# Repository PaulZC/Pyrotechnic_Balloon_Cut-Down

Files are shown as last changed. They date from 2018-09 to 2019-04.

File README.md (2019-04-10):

# Pyrotechnic Balloon Cut-Down Device

A lightweight wireless cut-down device for use on high altitude balloons.

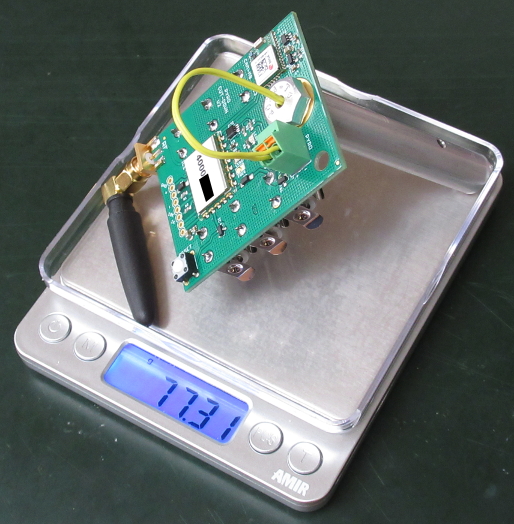
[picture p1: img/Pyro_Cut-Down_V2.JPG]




Designed to be triggered by the [Iridium Beacon Radio Board](https://github.com/PaulZC/Iridium_Beacon_Radio_Board) and equipped with an
[LPRS eRIC4 or eRIC9 integrated radio module](http://www.lprs.co.uk/products/easyradio-ism-modules/eric-soc-rf-modules.html),
the cut-down will be triggered when the eRIC receives its own (unique) serial number on the chosen channel. The number of cut-downs that could be
triggered by a single Iridium Beacon is essentially unlimited.

See [How do I configure the altitude limit](https://github.com/PaulZC/Pyrotechnic_Balloon_Cut-Down/blob/master/LEARN.md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)
for details on how to set the altitude limit using the I/O pins or via radio.

The cutter has been designed to reliably sever size 4N (2.4mm) braided nylon cord.

The cut-down device could also be used to control:
- a nichrome hot wire cord cutter
- a strobe or audible alarm
- any other device which can operate from 3.3V to 4.8V (depending on the battery voltage)

See [LEARN.md](https://github.com/PaulZC/Pyrotechnic_Balloon_Cut-Down/blob/master/LEARN.md) for further details.

See [ASSEMBLY.md](https://github.com/PaulZC/Pyrotechnic_Balloon_Cut-Down/blob/master/ASSEMBLY.md) for details on how to assemble and configure the PCB.

See [CUTTER.md](https://github.com/PaulZC/Pyrotechnic_Balloon_Cut-Down/blob/master/CUTTER.md) for details on how to assemble the mechanical parts.

See [Pyro_Cut-Down_V2.pdf](https://github.com/PaulZC/Pyrotechnic_Balloon_Cut-Down/blob/master/Pyro_Cut-Down_V2.pdf) for the schematic,
layout and Bill Of Materials.

The [Eagle](https://github.com/PaulZC/Pyrotechnic_Balloon_Cut-Down/tree/master/Eagle) directory contains the schematic and pcb design files.

The [eRIC](https://github.com/PaulZC/Pyrotechnic_Balloon_Cut-Down/tree/master/eRIC) directory contains the code for the eRIC integrated controller.

The [Drawings](https://github.com/PaulZC/Pyrotechnic_Balloon_Cut-Down/tree/master/Drawings) directory contains the drawings for the mechanical parts.

### Disclaimer

As this project involves the use of a very small quantity of smokeless gunpowder, the information contained herein should only be used by responsible adults
in full compliance with local laws and regulations regarding the purchase, transport, storage and use of smokeless powder. Follow the manufacturer's
instructions and safety information at all times. Appropriate Personal Protective Equipment must be used when handling gunpowder. Keep all parts of this
project out of the reach of children. Proceed entirely at your own risk.

The information contained herein is provided in good faith and is believed by the author to be both accurate and safe, but in no event shall the
author be liable for any injuries or damages resulting from the use of this information howsoever caused.

### Citation

If you have found this project useful and if you are able to, please cite the paper:

P. Clark et al, An open source toolkit for the tracking, termination and recovery of high altitude balloon flights and payloads, 2019 JINST 14 P04003
[DOI:10.1088/1748-0221/14/04/P04003](https://doi.org/10.1088/1748-0221/14/04/P04003)

The Accepted Manuscript is available on arXiv: http://arxiv.org/abs/1904.04321

### License

This project is distributed under a Creative Commons Attribution + Share-alike (BY-SA) licence.
Please refer to section 5 of the licence for the "Disclaimer of Warranties and Limitation of Liability".

Enjoy!

**_Paul_**

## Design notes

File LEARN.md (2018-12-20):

# Pyrotechnic Balloon Cut-Down Device

## LEARN

A lightweight wireless cut-down device for use on high altitude balloons.





Designed to be triggered by the [Iridium Beacon Radio Board](https://github.com/PaulZC/Iridium_Beacon_Radio_Board) and equipped with an
[LPRS eRIC4 or eRIC9 integrated radio module](http://www.lprs.co.uk/products/easyradio-ism-modules/eric-soc-rf-modules.html),
the cut-down will be triggered when the eRIC receives its own (unique) serial number on the chosen channel. The number of cut-downs that could be
triggered by a single Iridium Beacon is essentially unlimited.

**New for V2: the cut-down now includes a u-blox CAM-M8Q GNSS (GPS) receiver and can be configured to trigger at a pre-set altitude.**

The cutter has been designed to sever size 4N (2.4mm) braided nylon cord.

The cut-down device could also be used to control:
- a nichrome hot wire cord cutter
- a strobe or audible alarm
- any other device which can operate from 3.3V to 4.8V (depending on the battery voltage)

See [Pyro_Cut-Down_V2.pdf](https://github.com/PaulZC/Pyrotechnic_Balloon_Cut-Down/blob/master/Pyro_Cut-Down_V2.pdf) for the schematic,
layout and Bill Of Materials.

See [ASSEMBLY.md](https://github.com/PaulZC/Pyrotechnic_Balloon_Cut-Down/blob/master/ASSEMBLY.md) for details on how to assemble and configure the PCB.

The [Eagle](https://github.com/PaulZC/Pyrotechnic_Balloon_Cut-Down/tree/master/Eagle) directory contains the schematic and pcb design files.

The [eRIC](https://github.com/PaulZC/Pyrotechnic_Balloon_Cut-Down/tree/master/eRIC) directory contains the code for the eRIC integrated controller.

See [CUTTER.md](https://github.com/PaulZC/Pyrotechnic_Balloon_Cut-Down/blob/master/CUTTER.md) for details on how to assemble the mechanical parts.

The [Drawings](https://github.com/PaulZC/Pyrotechnic_Balloon_Cut-Down/tree/master/Drawings) directory contains the drawings for the mechanical parts.

### eRIC

The heart of the Cut-Down Device is the eRIC4 or eRIC9 [easyRadio Integrated Controller](http://www.lprs.co.uk/products/easyradio-ism-modules/eric-soc-rf-modules.html).

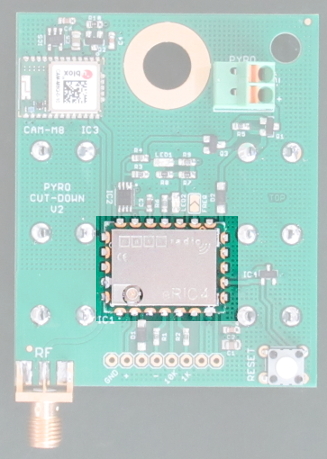
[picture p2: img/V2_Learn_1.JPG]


Either an eRIC4 or an eRIC9 can be installed. The eRIC4 operates at 402-470 MHz for Europe, APAC and China. The eRIC9 operates at 804-940 MHz for Europe,
North & South America, India and China. Solder the _FREQ_ split pad to select the eRIC9 915 MHz band.

Each eRIC has a unique serial number. The custom code running on the eRIC will trigger the cut-down when it receives a data packet containing that serial number.

The cut-down _PYRO_ output will be enabled when the eRIC receives:
- Its serial number
- Or its serial number followed by a "1"

Or, when it reaches the pre-configured altitude limit.

The cut-down output will be disabled when the eRIC receives:
- Its serial number followed by a "0"

If the serial number of the eRIC is _12345678_, the cut-down will be triggered when the eRIC receives either:
- _12345678_

or
- _123456781_

The cut-down output will be disabled when the eRIC receives:
- _123456780_

If you are using the [Iridium Beacon](https://github.com/PaulZC/Iridium_9603_Beacon) and the
[Iridium Beacon Radio Board](https://github.com/PaulZC/Iridium_Beacon_Radio_Board) to control the cut-down, you will need to send the commands:
- _[RADIO=12345678]_ or _[RADIO=123456781]_ to trigger the cut-down
- _[RADIO=123456780]_ to disable the cut-down

### u-blox CAM-M8Q

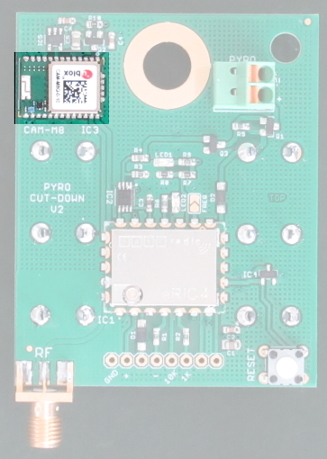
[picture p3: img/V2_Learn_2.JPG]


The cut-down is equipped with a u-blox CAM-M8Q GNSS (GPS) receiver which provides accurate altitude data.
To save power, the CAM-M8Q is configured to use only GPS satellites and ignores GLONASS, Galileo and BeiDou satellites.
Once the receiver has established a fix, the CAM-M8Q is put into low power mode to further extend the battery life.
The CAM-M8Q can be disabled by setting the altitude limit to 99km.

See [How do I configure the altitude limit](https://github.com/PaulZC/Pyrotechnic_Balloon_Cut-Down/blob/master/LEARN.md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)
below for details on how to set the altitude limit using the I/O pins or via radio.

### Pyrotechnic output

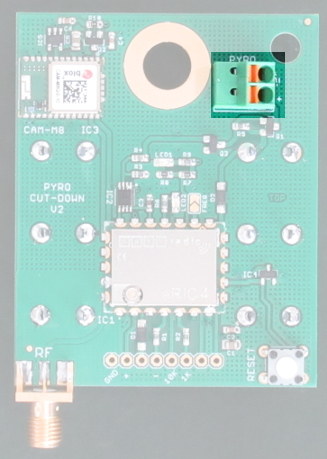
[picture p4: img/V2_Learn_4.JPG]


Q1 is a DMG3415U-7 P-Channel MOSFET which can switch currents of: 4 Amps continuous; 30 Amps pulsed. By default, the Gate of Q1 is held high by R5, which disables
the MOSFET. When the Gate of Q1 is pulled low by Q3, the full battery voltage is connected to the _PYRO+_ terminal, which triggers the electric
match within the pyrotechnic cutter.

Q3 is an NPN transistor. By default, the Base of Q3 is pulled low by R3, which disables the transistor and prevents it from pulling the Gate of Q1 low.
Q3 is enabled when the _FIRE_ signal connected to its Base goes high.

### Dual NOR gate

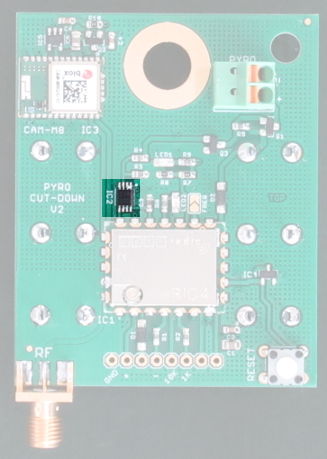
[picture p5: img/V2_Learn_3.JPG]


IC2 is a 7402 dual NOR logic gate. It prevents the _FIRE_ signal from accidentally going high, e.g. when the eRIC goes through a power-up reset. _FIRE_ can only
go high if:
- eRIC Pin17 is high (which provides power to the NOR gates)
- eRIC Pin18 is high
- eRIC Pin19 is low

The Input/Output pins on most microcontrollers go into a floating (high impedance) state during reset and can only be configured as outputs once the
embedded code starts to execute. The 7402 NOR gate ensures that _FIRE_ does not accidentally go high during that period.

### Reset supervisor

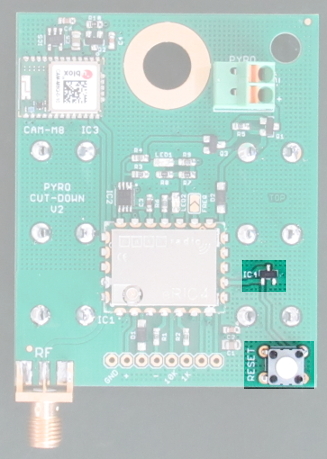
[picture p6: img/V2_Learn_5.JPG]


IC4 is an MCP111T-240 reset supervisor. It ensures that the eRIC is reset whenever the battery voltage falls below 2.4V.

Normally, the nichrome heating wire inside the electric match will go open-circuit as soon as the match is activated. If this fails to happen, Q1 will continue to
deliver current to the electric match until the batteries are exhausted. IC4 ensures that the eRIC is reset when the battery voltage starts to fall, which in turn
will disable Q1 via IC1 and Q3.

### LEDs

LED1 will illuminate when the PYRO output is active.

LED2 will flash once per second to show that the cut-down is operational. LED2 will be lit continuously when the eRIC is in bootloader mode.

### Diodes

D1 and D2 provide protection for the batteries and USB power pin from each other.

### I/O pins

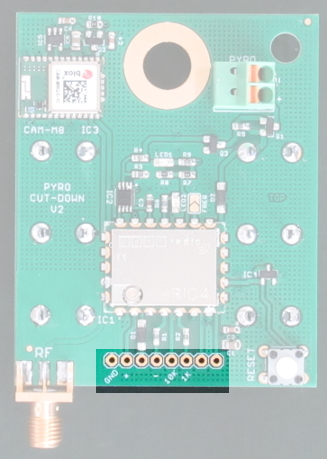
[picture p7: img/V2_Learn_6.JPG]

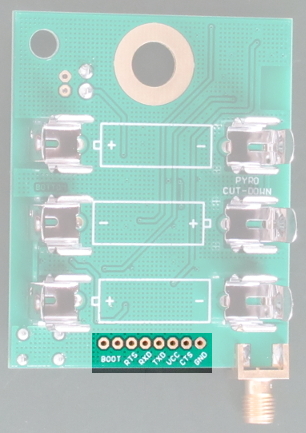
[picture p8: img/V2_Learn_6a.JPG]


The eRIC TxD, RxD, CTS and RTS pins are connected to 0.1" pads on the edge of the circuit board. The order of these pads matches the order of the pins of an FTDI
TTL-232R-3V3 USB to TTL serial cable. The eRIC can be reprogrammed via the FTDI cable.

Two extra pads are connected to the eRIC bootloader pins (Pin11 and Pin12). The eRIC will enter bootloader mode if these pads are shorted together on reset
or power-up. LED2 will be lit continuously when the eRIC is in bootloader mode.

### Antennas

Recommended antenna for the eRIC4 is:
- LPRS ANT-SR433 (Farnell part 2096221)

Recommended antenna for the eRIC9 is:
- LPRS ANT-SR900 (Farnell part 2096219)

http://www.lprs.co.uk/products/antennas-cables-connectors/stubby-antennas.html

The horizontal antenna orientation is important if the cut-down is positioned directly above the Iridium Beacon Radio Board on the balloon cord.

## How do I configure the altitude limit?

There are two methods to set the altitude limit: using the I/O pins; or via a radio message:

### Setting the Altitude Limit using the I/O pins:

The code enters Set_Altitude mode if the eRIC comes out of reset with the GND and PLUS pins connected together:
- Use a jumper wire to connect the GND and PLUS pins together;
- then press and release the RESET switch;
- then remove the jumper wire.
- The device will then enter Set_Altitude mode.



LED2 will flash three times to show that the digit three is selected.

Connect one end of the jumper wire to GND. Connect the other end to:
- MINUS to decrement the digit by one.
- PLUS to increment the digit by one.
- the 10K pin to store the digit as the altitude limit tens of kilometers.
- the 1K pin to store the digit as the altitude limit units of kilometers.

In the animation, the sequence of events is:
- The GND and PLUS pins are linked together
- The RESET switch is pressed and released
- The wire link is removed
- The cut-down is now in Set_Altitude mode
- The LED flashes three times to show the digit three
- The wire link is used to connect MINUS to GND once
- The LED flashes twice to show the digit two
- The wire link is used to connect 10K to GND once
- Two is stored in the altitude limit tens of kilometers and the LED gives a long flash
- The wire link is used to connect MINUS to GND once
- The LED flashes once to show the digit one
- The wire link is used to connect MINUS to GND once
- The LED stops flashing to show the digit zero
- The wire link is used to connect 1K to GND once
- Zero is stored in the altitude limit units of kilometers and the LED gives a long flash
- The altitude limit is now 20km
- The RESET switch is pressed and released
- The cut-down goes into normal operation
- The LED flashes twice, followed by a long flash, to indicate the altitude limit is 20km

The eRIC will stay in Set_Altitude mode until reset. Always reset the eRIC to start normal operation.

To disable the altitude limit, set it to 99km. This causes the CAM-M8Q GNSS receiver to be switched completely off,
significantly extending the battery life.

### Setting the Altitude Limit using a Radio Message:

Each eRIC has a unique serial number. The custom code running on the eRIC will set the altitude limit when it receives a data packet containing:
the eRIC serial number; followed by a "2"; followed by two digits which represent the altitude limit is kilometres.

If the serial number of the eRIC is _12345678_, an altitude limit of 33km (33000m) will be set when the eRIC receives:
- _12345678233_

If you are using the [Iridium Beacon](https://github.com/PaulZC/Iridium_9603_Beacon) and the
[Iridium Beacon Radio Board](https://github.com/PaulZC/Iridium_Beacon_Radio_Board) to control the cut-down, you will need to set the altitude limit via a RADIO command.

If you want to set the altitude limit to 33km (33000m), send:
- _[RADIO=12345678233]_

To set the altitude limit to 1km (1000m), send:
- _[RADIO=12345678201]_

The altitude limit can be disabled by setting it to 99km. This causes the CAM-M8Q GNSS receiver to be switched completely off, significantly extending the battery life.
Send:
- _[RADIO=12345678299]_

The altitude limit can be re-enabled by setting it to anything other than 99km.

## The LED flashes when I connect the batteries or reset the eRIC. Why?

When the batteries are connected or the reset switch is pressed, the cut-down goes into normal operation. The LED flashes to indicate the altitude limit. The default is
33km so the LED will flash three times, pause, then flash three times again.

A zero is indicated by a long flash. Two flashes followed by a long flash indicates an altitude limit of 20km.
A long flash followed by one flash indicates a limit of 1km.

To test that the CAM-M8Q is operating correctly, try setting an altitude limit of 0km (indicated by two long flashes).
The PYRO output and LED1 will be enabled as soon as a GPS signal is acquired (unless you are below sea level!).

## How much does it weigh?



The total weight of the assembled cut-down is 77.3 grams. This comprises:
- Assembled cutter: 27.2g
- Energiser® Ultimate Lithium AAA batteries: 22.7g
- Assembled circuit board: 21.0g
- Antenna: 6.4g

## Which AAA batteries should I use?
Energiser® Ultimate Lithium batteries. These are rated down to -40°C but tests I've done (using dry ice) show that they continue to work much colder than that.

## How long will the batteries last?

With the CAM-M8Q disabled, the average current draw is 4.6mA at 4.5V. When powered by three Energiser® Ultimate Lithium AAA batteries, the batteries
should last approximately 10 days. This ignores the current drawn by the electric match when the cut-down is activated.

With the CAM-M8Q enabled, the battery life will be reduced to approximately 2 days.

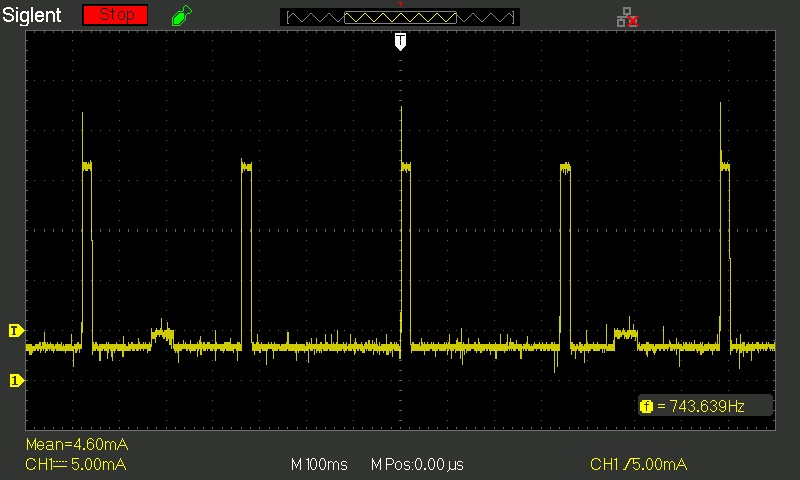
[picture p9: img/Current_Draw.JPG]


## Do I need to be careful around the battery clips?

Yes! The clips are of course conductive. If you place the circuit board battery-side down on a conductive surface **BAD THINGS WILL HAPPEN!**

## Have you tested it?

Yes. The cutter has been used successfully to sever size 4N (2.4mm) braided nylon cord with test loads of 2kg and 100g.

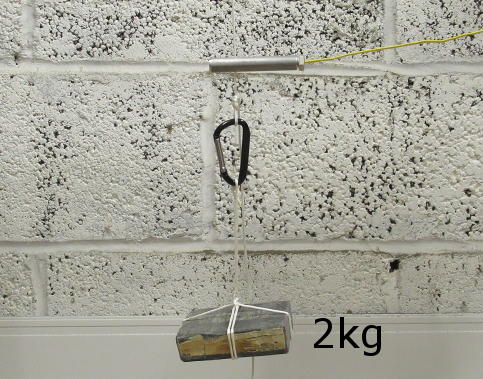
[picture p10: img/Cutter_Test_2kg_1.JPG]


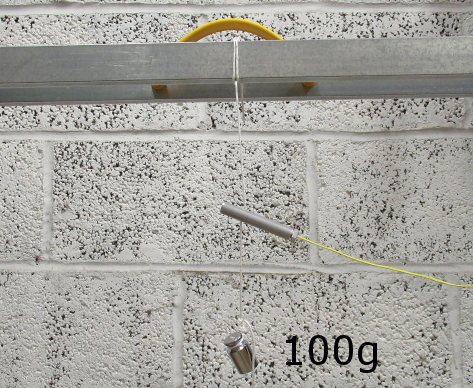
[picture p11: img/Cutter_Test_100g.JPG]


## License

This project is distributed under a Creative Commons Attribution + Share-alike (BY-SA) licence.
Please refer to section 5 of the licence for the "Disclaimer of Warranties and Limitation of Liability".

Enjoy!

**_Paul_**

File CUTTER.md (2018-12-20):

# Pyrotechnic Balloon Cut-Down Device

## Cutter Assembly

A lightweight wireless cut-down device for use on high altitude balloons.

The cutter has been designed to reliably sever size 4N (2.4mm) braided nylon cord.



### Drawings

The [Drawings](https://github.com/PaulZC/Pyrotechnic_Balloon_Cut-Down/tree/master/Drawings) directory contains the drawings for the mechanical parts plus an
assembly drawing.

### Use and Storage

Prepare the cutter as close as possible to the time of your flight, to minimise the possibility of the powder becoming damp.

If this is not possible, store the assembled cutter in a sealed box with a large sachet of fresh dessiccant.

### Prepare the Electric Match

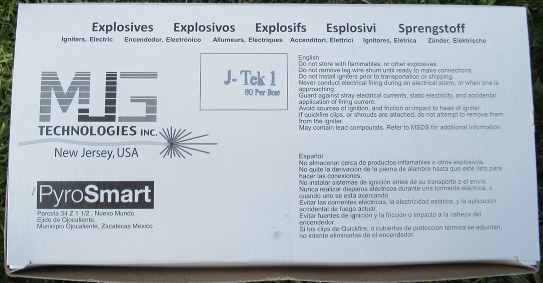
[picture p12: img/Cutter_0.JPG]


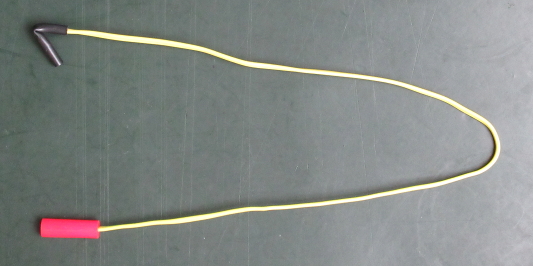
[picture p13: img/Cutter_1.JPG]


The cutter is ignited by an [MJG Technologies J-Tek1 igniter](https://electricmatch.com/pyrotechnics/see/9/5/j-tek-igniter). Made in the USA, these
are readily available from fireworks display suppliers in many countries including the UK. Technical information is available on the
[MJG Technologies website](https://electricmatch.com/upload/JTEK_TECHNICAL_INFORMATION_SHEET_SPECIFICATIONS.PDF).

The igniter contains a 1.0 ohm nichrome wire which, when heated by a current of 1 Amp or more, ignites the pyrotechnic 'match head'. The J-Tek1 can be
triggered by a single AAA alkaline battery.

Remove the black protective cover from the end of the igniter wires and ensure the bare copper wires are twised securely together. This shorts the
igniter, preventing it from being ignited accidentally by a static discharge.

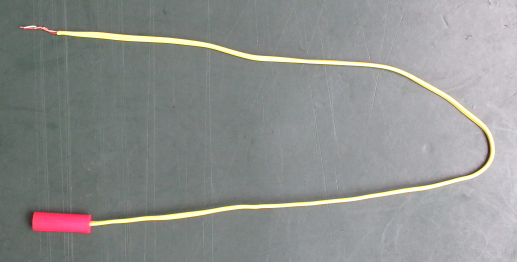
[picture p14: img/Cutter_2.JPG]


Remove the red plastic cover by pushing it off the match head and sliding it along the wire.

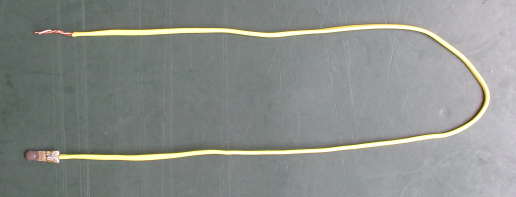
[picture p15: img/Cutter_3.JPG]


Slide a McMaster 1173N004 silicone o-ring (0.070" internal diameter) along the igniter wire until it almost touches the solder joint. This o-ring will
help prevent the gas from the powder escaping through the hex head screw.

Slide a McMaster 1173N005 silicone o-ring (0.101" ID) over the match head as shown in the assembly drawing. This o-ring will prevent the igniter from making
electrical contact with the conductive aluminium cutter body.

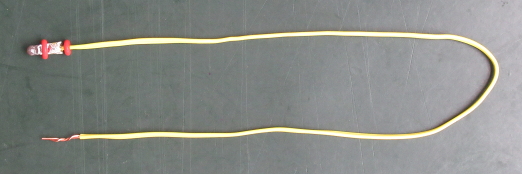
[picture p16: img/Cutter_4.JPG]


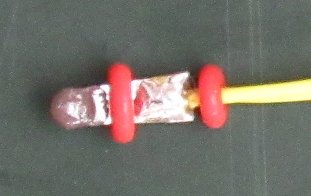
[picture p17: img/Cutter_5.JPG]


Poke the bare ends of the wires through a McMaster 93306A580 aluminium hex head screw, which has been drilled through with a 7/64" (2.8mm) drill bit. Slide the
screw along the wires until it touches the smaller o-ring.

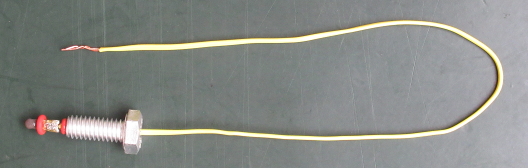
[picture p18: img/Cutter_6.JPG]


Keep the igniter wires shorted together until the cutter is complete and you are ready to connect it to the cut-down circuit board.

### Add the Smokeless Powder

Check that the inside of the cutter body is clean, dry and free from debris. Clean it with a cotton swab dipped in alcohol (rubbing alcohol or Isopropyl
Alcohol (IPA)) if required. Use a size F reamer (McMaster 89485A46) by hand to clear any stubborn deposits or burrs from the cord holes.

Insert a paper clip through the cord holes and bend it to prevent it falling out.

Slide a clean McMaster 98105A090 dowel pin into the cutter body, inserting the flatter end first. The paper clip prevents the dowel pin from sliding past the cord
holes.

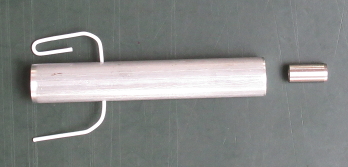
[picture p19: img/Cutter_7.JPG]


Stand the cutter body upright and using a small funnel (normally used to refill perfume bottles), pour 1.5 grains (0.10 grams) of smokeless powder into the cutter
body so it ends up on top of the dowel pin. Ensure the funnel is clean and dry before use. 0.10 grams of powder is the same amount found inside a Fiocchi 8mm NIK
starting pistol blank.

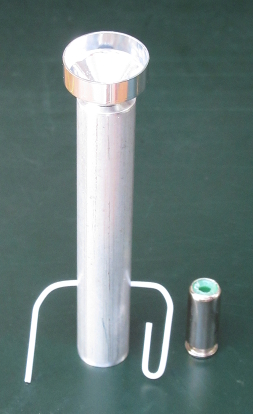
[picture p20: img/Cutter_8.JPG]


### Assemble the Cutter

Feed the igniter assembly through the cut-down circuit board and then screw it carefully into the cutter body. Orient the holes in the cutter body so they
are vertical with respect to the circuit board, then tighten the screw using a spanner. Do not overtighten the screw.

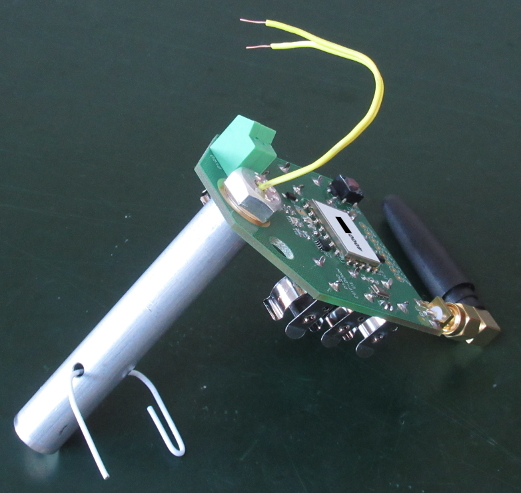
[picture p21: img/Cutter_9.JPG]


### Connect the Cutter

Cut the igniter wires short. Part the wires and remove 5mm of insulation from the end of each wire. Push the bare wire ends into the green terminal block
on the cut-down circuit board. You do not need to press the orange levers on the terminal block while you do this. The levers only need to be pressed when
releasing the wires.

Your cutter is ready for use.

You may need to melt and shape the cut end of the nylon cord so it will slide easily through the cord holes.

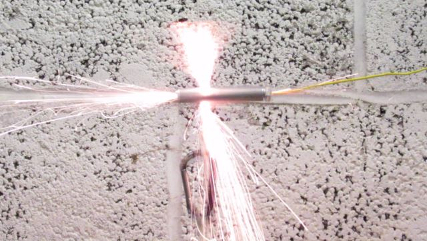
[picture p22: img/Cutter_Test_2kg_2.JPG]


### Reuse

After use, the dowel pin will end up trapped at the end of the cutter body, almost certainly jammed in place by remnants of nylon cord. You may need to drive
a parallel pin punch (McMaster 3416A24) into the hole in the end of the cutter body to release it. Take care to hold the pin punch on axis so as not to damage
the reamed bore of the cutter body.

Clean the dowel pin with cotton wool dipped in alcohol (rubbing alcohol or IPA). Clean the cutter body with a cotton swab dipped in alcohol.

Use a size F reamer (McMaster 89485A46) by hand to clear any stubborn deposits or burrs from the cord holes.

Use new o-rings each time even if they look intact.

### Disclaimer

As this project involves the use of a very small quantity of smokeless gunpowder, the information contained herein should only be used by responsible adults
in full compliance with local laws and regulations regarding the purchase, transport, storage and use of smokeless powder. Follow the manufacturer's
instructions and safety information at all times. Appropriate Personal Protective Equipment must be used when handling gunpowder. Keep all parts of this
project out of the reach of children. Proceed entirely at your own risk.

The information contained herein is provided in good faith and is believed by the author to be both accurate and safe, but in no event shall the
author be liable for any injuries or damages resulting from the use of this information howsoever caused.

### License

This project is distributed under a Creative Commons Attribution + Share-alike (BY-SA) licence.
Please refer to section 5 of the licence for the “Disclaimer of Warranties and Limitation of Liability”.

Enjoy!

**_Paul_**

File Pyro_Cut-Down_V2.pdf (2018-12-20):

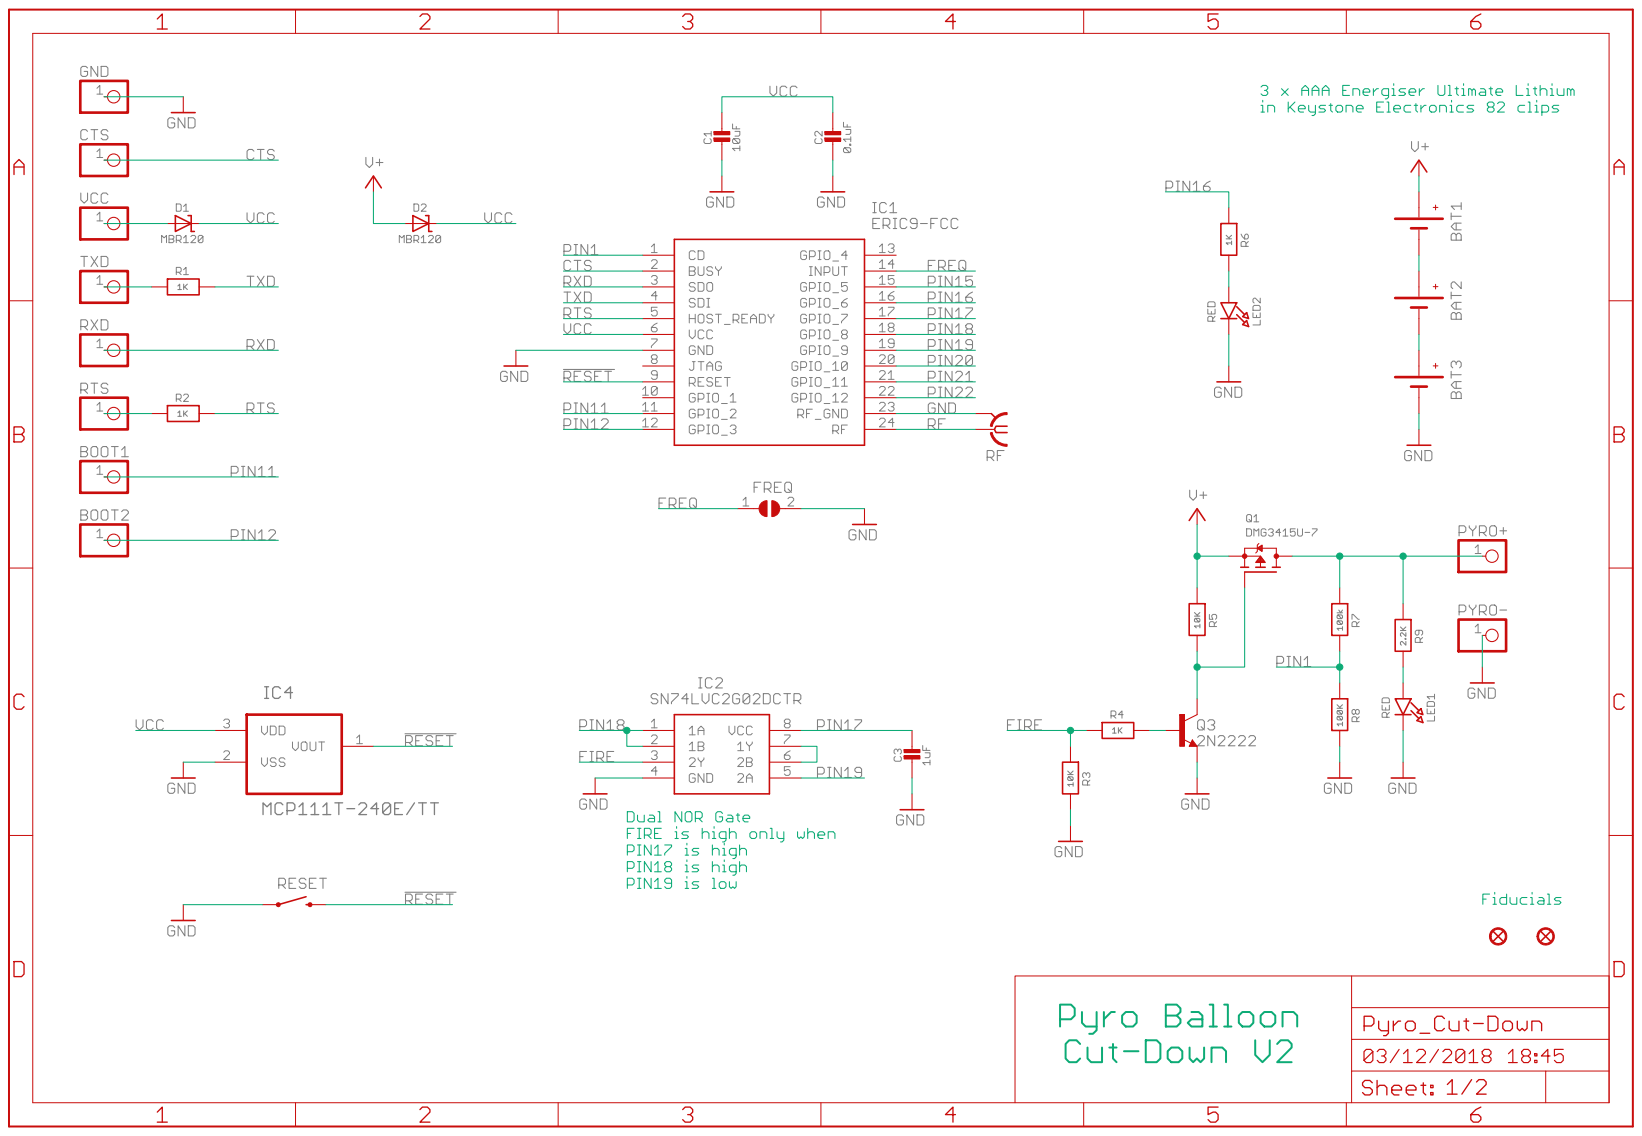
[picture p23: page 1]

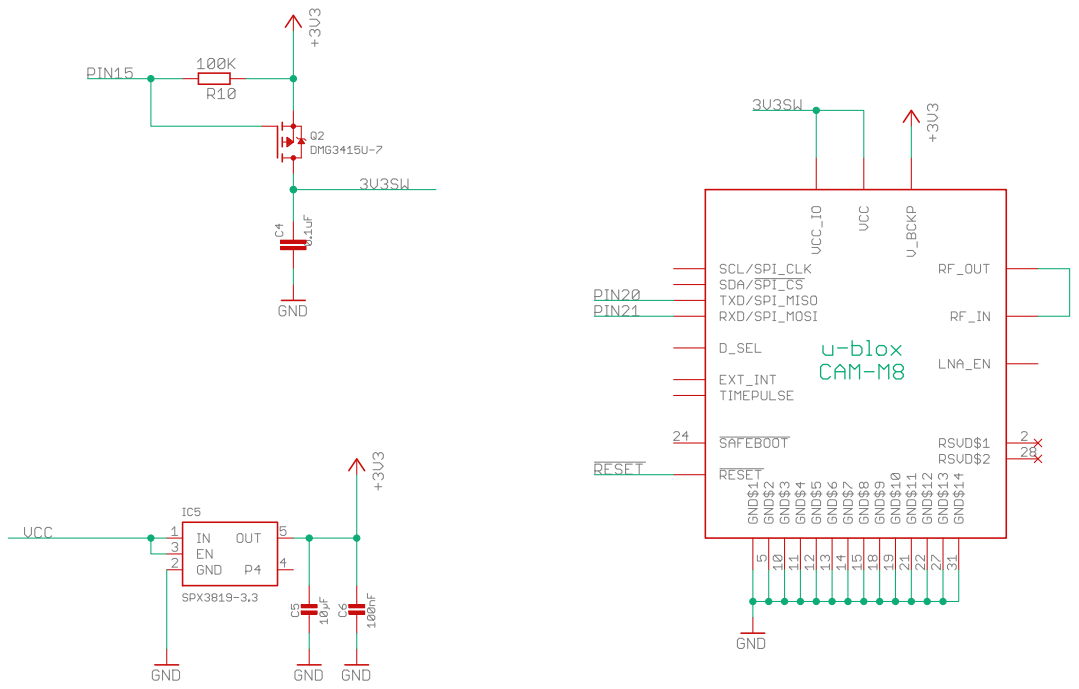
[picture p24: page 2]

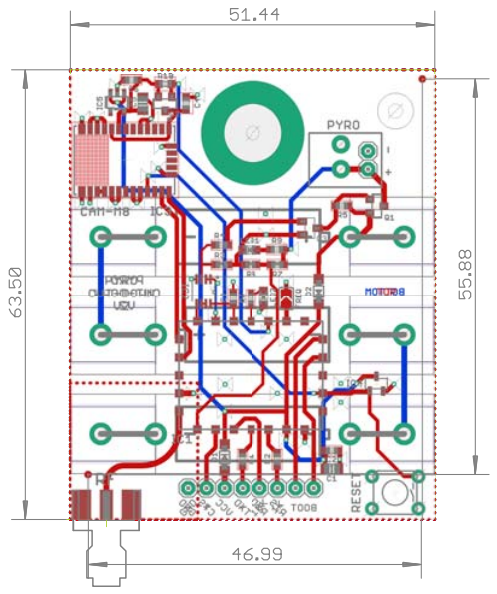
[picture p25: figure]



Part | X | Y | Angle | Package | Value | Manufacturer | Manufacturer Part No | Farnell Part No Mouser Part No | Description
Dimensions 51.44 | 63.50

Fiducials - for solder paste mask alignment:

FD1 | 49.53 | 62.23 | | | | | | | | Fiducial 1mm
FD2 | 2.54 | 6.35 | | | | | | | | Fiducial 1mm

Surface Mount Components:

C1 | 36.83 | 7.18 | 0 | 0805 | 10uF | Murata | GCJ21BR71A106KE01L | 2781411 | | MultiLayer Ceramic Capacitor; 10uF; 10V; 0805; X7R
C2 | 36.83 | 9.72 | 0 | 0603 | 0.1uF | Murata | GRM188R71H104JA93D 2688523 | MultiLayer Ceramic Capacitor; 0.1uF; 50V; 0603; X7R
C3 | 22.76 | 31.21 | 90 | 0603 | 1uF | Murata | GRM188R61A105KA61D 1828798 | MultiLayer Ceramic Capacitor; 1uF; 10V; 0603; X5R
C4 | 16.19 | 58.80 | 90 | 0603 | 0.1uF | Murata | GRM188R71H104JA93D 2688523 | MultiLayer Ceramic Capacitor; 0.1uF; 50V; 0603; X7R
C5 | 10.16 | 58.74 | 90 | 0805 | 10uF | Murata | GCJ21BR71A106KE01L | 2781411 | | MultiLayer Ceramic Capacitor; 10uF; 10V; 0805; X7R
C6 | 8.57 | 62.10 | 180 | 0603 | 0.1uF | Murata | GRM188R71H104JA93D 2688523 | MultiLayer Ceramic Capacitor; 0.1uF; 50V; 0603; X7R
D1 | 21.59 | 8.76 | 270 | SOD-123 | MBR120 | ON SEMICONDUCTOR MBR120VLSFT1G | 1431044 | Schottky Rectifier; 20V; 1A; SOD-123
D2 | 34.99 | 32.23 | 90 | SOD-123 | MBR120 | ON SEMICONDUCTOR MBR120VLSFT1G | 1431044 | Schottky Rectifier; 20V; 1A; SOD-123
IC1 | 25.4 | 20.32 | 0 | | ERIC4 | LPRS | ERIC4 | 2362439 | | LPRS easy Radio Intelligent Controller 433MHz
| | | | | ERIC9 | LPRS | ERIC9 | 2362440 | | LPRS easy Radio Intelligent Controller 868/915MHz
IC2 | 18.64 | 32.23 | 270 | SOP65P400X130-8N SN74LVC2G02DCTR Texas Instruments | SN74LVC2G02DCTR | 1236358 | NOR Gate, 2 Input, 32 mA, 1.65 V to 5.5 V, SSOP-8
IC3 | 7.95 | 50.8 | 180 | | CAM-M8Q | u-blox | CAM-M8Q | | | https://www.u-blox.com/en/product/cam-m8-series
IC4 | 43.08 | 19.15 | 0 | SOT23-3 | MCP111T-240E/TT | Microchip | MCP111T-240E/TT | 1627192 | | Reset Supervisor; SOT23-3; 2.40V; Open Drain; Active Low
IC5 | 6.6 | 58.93 | 180 | SOT23-5 | SPX3819-3.3 | Exar | SPX3819M5-L-3-3/TR | | 701-SPX3819M5-L-33TR | LDO Voltage Regulator; 500mA; SOT-23-5
LED1 | 25.15 | 38.16 | 90 | 2.0x1.25 | RED | Wurth Electronik | 150080RS75000 | 2322077 | 710-150080RS75000 | LED; Red; 20mA; 2V; 2.0x1.25mm
LED2 | 27.24 | 31.34 | 180 | 2.0x1.25 | RED | Wurth Electronik | 150080RS75000 | 2322077 | 710-150080RS75000 | LED; Red; 20mA; 2V; 2.0x1.25mm
Q1 | 43.15 | 44.35 | 270 | SOT23 | DMG3415U-7 | Diodes Inc. | DMG3415U-7 | 1843688 | | MOSFET; P Channel; SOT23-WIDE
Q2 | 13.27 | 58.74 | 180 | SOT23 | DMG3415U-7 | Diodes Inc. | DMG3415U-7 | 1843688 | | MOSFET; P Channel; SOT23-WIDE
Q3 | 33.75 | 41.24 | 270 | SOT23 | 2N2222 | Fairchild | MMBT2222A | 9846700 | | Bipolar (BJT) Single Transistor, NPN, 40 V, 350 mW, 1 A
R1 | 24.07 | 8.51 | 90 | 0603 | 1K | Multicomp | MCWR06X1001FTL | 2447272 | | Chip Resistor; Thick Film; 1k; 50V; 0603; 100mW
R2 | 29.15 | 8.51 | 90 | 0603 | 1K | Multicomp | MCWR06X1001FTL | 2447272 | | Chip Resistor; Thick Film; 1k; 50V; 0603; 100mW
R3 | 21.18 | 36.1 | 0 | 0603 | 10K | Multicomp | MCWR06X1002FTL | 2447230 | | Chip Resistor; Thick Film; 10k; 50V; 0603; 100mW
R4 | 21.15 | 38.86 | 0 | 0603 | 1K | Multicomp | MCWR06X1001FTL | 2447272 | | Chip Resistor; Thick Film; 1k; 50V; 0603; 100mW
R5 | 38.23 | 44.39 | 180 | 0603 | 10K | Multicomp | MCWR06X1002FTL | 2447230 | | Chip Resistor; Thick Film; 10k; 50V; 0603; 100mW
R6 | 25.37 | 31.15 | 90 | 0603 | 1K | Multicomp | MCWR06X1001FTL | 2447272 | | Chip Resistor; Thick Film; 1k; 50V; 0603; 100mW
R7 | 29.18 | 36.1 | 180 | 0603 | 100K | Multicomp | MCWR06X1003FTL | 2447226 | | Chip Resistor; Thick Film; 100k; 50V; 0603; 100mW
R8 | 25.3 | 36.1 | 180 | 0603 | 100K | Multicomp | MCWR06X1003FTL | 2447226 | | Chip Resistor; Thick Film; 100k; 50V; 0603; 100mW
R9 | 29.11 | 38.26 | 180 | 0603 | 2.2K | Multicomp | MCWR06X2201FTL | 2447320 | | Chip Resistor; Thick Film; 2.2k; 50V; 0603; 100mW
R10 | 13.27 | 61.53 | 0 | 0603 | 100k | Multicomp | MCWR06X1003FTL | 2447226 | | Chip Resistor; Thick Film; 100k; 50V; 0603; 100mW

Non-surface mount components:

RF | | | | | SMA Jack | Johnson | 142-0711-821 | 1019328 | | SMA End Launch Jack
BAT1 | AAA-Clip_Pair | Keystone Electronics 82 | 908721 | Keystone Electronics 82 AAA Battery Clip (Pair)
BAT2 | AAA-Clip_Pair | Keystone Electronics 82 | 908721 | Keystone Electronics 82 AAA Battery Clip (Pair)
BAT3 | AAA-Clip_Pair | Keystone Electronics 82 | 908721 | Keystone Electronics 82 AAA Battery Clip (Pair)
RESET | | | | | Tactile Switch | Multicomp | MCDTS6-1N | 9471685 | | Switch, SPST, 0.05A, 12VDC, 160gf
PYRO | | | | | Terminal Block | Phoenix Contact | SPTA 1/2-3.5 | 1793729 | | Terminal Block; 3.5mm; 2 Ways; 24-16 AWG

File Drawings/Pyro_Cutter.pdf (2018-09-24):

Ø½” Nominal

A | A

Section A-A; Drill Ø¼” Ream to Ø0.257" (Size F); 5/16"-18 (UNC)

## Pyro Line Cutter

## Use Ø½” 7075 T6 Aluminium Rod (McMaster Part No. 90465K73)

Ø¼” x ½” Undersized Dowel Pin (McMaster Part 98105A090); MJG Technologies (ElectricMatch.com) J-Tek1 Igniter; 5/16"-18 x ¾” Aluminium Hex Head Screw (McMaster Part 93306A580) Drilled through Ø; Keep igniter wires shorted until ready to connect to cut-down unit; Silicone O-Ring with 0.070" ID (McMaster Part 1173N004); Silicone O-Ring with 0.101" ID (McMaster Part 1173N005); 1.5 grains (0.10g) smokeless powder

## Pyro Line Cutter Assembly

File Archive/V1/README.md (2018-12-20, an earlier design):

# Pyrotechnic Balloon Cut-Down Device

A lightweight wireless cut-down device for use on high altitude balloons.





Designed to be triggered by the [Iridium Beacon Radio Board](https://github.com/PaulZC/Iridium_Beacon_Radio_Board) and equipped with an
[LPRS eRIC4 or eRIC9 integrated radio module](http://www.lprs.co.uk/products/easyradio-ism-modules/eric-soc-rf-modules.html),
the cut-down will be triggered when the eRIC receives its own (unique) serial number on the chosen channel. The number of cut-downs that could be
triggered by a single Iridium Beacon is essentially unlimited.

The cutter has been designed to reliably sever size 4N (2.4mm) braided nylon cord.

The cut-down device could also be used to control:
- a nichrome hot wire cord cutter
- a strobe or audible alarm
- any other device which can operate from 3.3V to 4.8V (depending on the battery voltage)

See [LEARN.md](https://github.com/PaulZC/Pyrotechnic_Balloon_Cut-Down/blob/master/Archive/V1/LEARN.md) for further details.

See [ASSEMBLY.md](https://github.com/PaulZC/Pyrotechnic_Balloon_Cut-Down/blob/master/Archive/V1/ASSEMBLY.md) for details on how to assemble and configure the PCB.

See [CUTTER.md](https://github.com/PaulZC/Pyrotechnic_Balloon_Cut-Down/blob/master/Archive/V1/CUTTER.md) for details on how to assemble the mechanical parts.

See [Pyro_Cut-Down_V1.pdf](https://github.com/PaulZC/Pyrotechnic_Balloon_Cut-Down/blob/master/Archive/V1/Pyro_Cut-Down_V1.pdf) for the schematic,
layout and Bill Of Materials.

The [Eagle](https://github.com/PaulZC/Pyrotechnic_Balloon_Cut-Down/tree/master/Archive/V1/Eagle) directory contains the schematic and pcb design files.

The [eRIC](https://github.com/PaulZC/Pyrotechnic_Balloon_Cut-Down/tree/master/Archive/V1/eRIC) directory contains the code for the eRIC integrated controller.

The [Drawings](https://github.com/PaulZC/Pyrotechnic_Balloon_Cut-Down/tree/master/Archive/V1/Drawings) directory contains the drawings for the mechanical parts.

### Disclaimer

As this project involves the use of a very small quantity of smokeless gunpowder, the information contained herein should only be used by responsible adults
in full compliance with local laws and regulations regarding the purchase, transport, storage and use of smokeless powder. Follow the manufacturer's
instructions and safety information at all times. Appropriate Personal Protective Equipment must be used when handling gunpowder. Keep all parts of this
project out of the reach of children. Proceed entirely at your own risk.

The information contained herein is provided in good faith and is believed by the author to be both accurate and safe, but in no event shall the
author be liable for any injuries or damages resulting from the use of this information howsoever caused.

### License

This project is distributed under a Creative Commons Attribution + Share-alike (BY-SA) licence.
Please refer to section 5 of the licence for the "Disclaimer of Warranties and Limitation of Liability".

Enjoy!

**_Paul_**

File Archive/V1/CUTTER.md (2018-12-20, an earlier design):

# Pyrotechnic Balloon Cut-Down Device

## Cutter Assembly

A lightweight wireless cut-down device for use on high altitude balloons.

The cutter has been designed to reliably sever size 4N (2.4mm) braided nylon cord.



### Drawings

The [Drawings](https://github.com/PaulZC/Pyrotechnic_Balloon_Cut-Down/tree/master/Archive/V1/Drawings) directory contains the drawings for the mechanical parts plus an
assembly drawing.

### Use and Storage

Prepare the cutter as close as possible to the time of your flight, to minimise the possibility of the powder becoming damp.

If this is not possible, store the assembled cutter in a sealed box with a large sachet of fresh dessiccant.

### Prepare the Electric Match





The cutter is ignited by an [MJG Technologies J-Tek1 igniter](https://electricmatch.com/pyrotechnics/see/9/5/j-tek-igniter). Made in the USA, these
are readily available from fireworks display suppliers in many countries including the UK. Technical information is available on the
[MJG Technologies website](https://electricmatch.com/upload/JTEK_TECHNICAL_INFORMATION_SHEET_SPECIFICATIONS.PDF).

The igniter contains a 1.0 ohm nichrome wire which, when heated by a current of 1 Amp or more, ignites the pyrotechnic 'match head'. The J-Tek1 can be
triggered by a single AAA alkaline battery.

Remove the black protective cover from the end of the igniter wires and ensure the bare copper wires are twised securely together. This shorts the
igniter, preventing it from being ignited accidentally by a static discharge.



Remove the red plastic cover by pushing it off the match head and sliding it along the wire.



Slide a McMaster 1173N004 silicone o-ring (0.070" internal diameter) along the igniter wire until it almost touches the solder joint. This o-ring will
help prevent the gas from the powder escaping through the hex head screw.

Slide a McMaster 1173N005 silicone o-ring (0.101" ID) over the match head as shown in the assembly drawing. This o-ring will prevent the igniter from making
electrical contact with the conductive aluminium cutter body.





Poke the bare ends of the wires through a McMaster 93306A580 aluminium hex head screw, which has been drilled through with a 7/64" (2.8mm) drill bit. Slide the
screw along the wires until it touches the smaller o-ring.



Keep the igniter wires shorted together until the cutter is complete and you are ready to connect it to the cut-down circuit board.

### Add the Smokeless Powder

Check that the inside of the cutter body is clean, dry and free from debris. Clean it with a cotton swab dipped in alcohol (rubbing alcohol or Isopropyl
Alcohol (IPA)) if required. Use a size F reamer (McMaster 89485A46) by hand to clear any stubborn deposits or burrs from the cord holes.

Insert a paper clip through the cord holes and bend it to prevent it falling out.

Slide a clean McMaster 98105A090 dowel pin into the cutter body, inserting the flatter end first. The paper clip prevents the dowel pin from sliding past the cord
holes.



Stand the cutter body upright and using a small funnel (normally used to refill perfume bottles), pour 1.5 grains (0.10 grams) of smokeless powder into the cutter
body so it ends up on top of the dowel pin. Ensure the funnel is clean and dry before use. 0.10 grams of powder is the same amount found inside a Fiocchi 8mm NIK
starting pistol blank.



### Assemble the Cutter

Feed the igniter assembly through the cut-down circuit board and then screw it carefully into the cutter body. Orient the holes in the cutter body so they
are vertical with respect to the circuit board, then tighten the screw using a spanner. Do not overtighten the screw.



### Connect the Cutter

Cut the igniter wires short. Part the wires and remove 5mm of insulation from the end of each wire. Push the bare wire ends into the green terminal block
on the cut-down circuit board. You do not need to press the orange levers on the terminal block while you do this. The levers only need to be pressed when
releasing the wires.



Your cutter is ready for use.

You may need to melt and shape the cut end of the nylon cord so it will slide easily through the cord holes.



### Reuse

After use, the dowel pin will end up trapped at the end of the cutter body, almost certainly jammed in place by remnants of nylon cord. You may need to drive
a parallel pin punch (McMaster 3416A24) into the hole in the end of the cutter body to release it. Take care to hold the pin punch on axis so as not to damage
the reamed bore of the cutter body.

Clean the dowel pin with cotton wool dipped in alcohol (rubbing alcohol or IPA). Clean the cutter body with a cotton swab dipped in alcohol.

Use a size F reamer (McMaster 89485A46) by hand to clear any stubborn deposits or burrs from the cord holes.

Use new o-rings each time even if they look intact.

### Disclaimer

As this project involves the use of a very small quantity of smokeless gunpowder, the information contained herein should only be used by responsible adults
in full compliance with local laws and regulations regarding the purchase, transport, storage and use of smokeless powder. Follow the manufacturer's
instructions and safety information at all times. Appropriate Personal Protective Equipment must be used when handling gunpowder. Keep all parts of this
project out of the reach of children. Proceed entirely at your own risk.

The information contained herein is provided in good faith and is believed by the author to be both accurate and safe, but in no event shall the
author be liable for any injuries or damages resulting from the use of this information howsoever caused.

### License

This project is distributed under a Creative Commons Attribution + Share-alike (BY-SA) licence.
Please refer to section 5 of the licence for the “Disclaimer of Warranties and Limitation of Liability”.

Enjoy!

**_Paul_**

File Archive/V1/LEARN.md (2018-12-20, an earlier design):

# Pyrotechnic Balloon Cut-Down Device

## LEARN

A lightweight wireless cut-down device for use on high altitude balloons.





Designed to be triggered by the [Iridium Beacon Radio Board](https://github.com/PaulZC/Iridium_Beacon_Radio_Board) and equipped with an
[LPRS eRIC4 or eRIC9 integrated radio module](http://www.lprs.co.uk/products/easyradio-ism-modules/eric-soc-rf-modules.html),
the cut-down will be triggered when the eRIC receives its own (unique) serial number on the chosen channel. The number of cut-downs that could be
triggered by a single Iridium Beacon is essentially unlimited.

The cutter has been designed to sever size 4N (2.4mm) braided nylon cord.

The cut-down device could also be used to control:
- a nichrome hot wire cord cutter
- a strobe or audible alarm
- any other device which can operate from 3.3V to 4.8V (depending on the battery voltage)

See [Pyro_Cut-Down_V1.pdf](https://github.com/PaulZC/Pyrotechnic_Balloon_Cut-Down/blob/master/Archive/V1/Pyro_Cut-Down_V1.pdf) for the schematic,
layout and Bill Of Materials.

See [ASSEMBLY.md](https://github.com/PaulZC/Pyrotechnic_Balloon_Cut-Down/blob/master/Archive/V1/ASSEMBLY.md) for details on how to assemble and configure the PCB.

The [Eagle](https://github.com/PaulZC/Pyrotechnic_Balloon_Cut-Down/tree/master/Archive/V1/Eagle) directory contains the schematic and pcb design files.

The [eRIC](https://github.com/PaulZC/Pyrotechnic_Balloon_Cut-Down/tree/master/Archive/V1/eRIC) directory contains the code for the eRIC integrated controller.

See [CUTTER.md](https://github.com/PaulZC/Pyrotechnic_Balloon_Cut-Down/blob/master/Archive/V1/CUTTER.md) for details on how to assemble the mechanical parts.

The [Drawings](https://github.com/PaulZC/Pyrotechnic_Balloon_Cut-Down/tree/master/Archive/V1/Drawings) directory contains the drawings for the mechanical parts.

### eRIC

The heart of the Cut-Down Device is the eRIC4 or eRIC9 [easyRadio Integrated Controller](http://www.lprs.co.uk/products/easyradio-ism-modules/eric-soc-rf-modules.html).



Either an eRIC4 or an eRIC9 can be installed. The eRIC4 operates at 402-470 MHz for Europe, APAC and China. The eRIC9 operates at 804-940 MHz for Europe,
North & South America, India and China. Solder the _FREQ_ split pad to select the eRIC9 915 MHz band.

Each eRIC has a unique serial number. The custom code running on the eRIC will trigger the cut-down when it receives a data packet containing that serial number.

The cut-down _PYRO_ output will be enabled when the eRIC receives:
- Its serial number
- Or its serial number followed by a "1"

The cut-down output will be disabled when the eRIC receives:
- Its serial number followed by a "0"

If the serial number of the eRIC is _12345678_, the cut-down will be triggered when the eRIC receives either:
- _12345678_

or
- _123456781_

The cut-down output will be disabled when the eRIC receives:
- _123456780_

If you are using the [Iridium Beacon](https://github.com/PaulZC/Iridium_9603_Beacon) and the
[Iridium Beacon Radio Board](https://github.com/PaulZC/Iridium_Beacon_Radio_Board) to control the cut-down, you will need to send the commands:
- _[RADIO=12345678]_ or _[RADIO=123456781]_ to trigger the cut-down
- _[RADIO=123456780]_ to disable the cut-down

### MPL3115A2



The cut-down can be equipped with an (optional) MPL3115A2 pressure and temperature sensor. The pressure reading can be converted into altitude using the equation
given in the [MPL3115A2 datasheet](https://www.nxp.com/docs/en/data-sheet/MPL3115A2.pdf) or, more accurately, using the
[Barometric Formula](https://en.wikipedia.org/wiki/Barometric_formula).

Even if the Barometric Formula is used, altitudes above 15km could have an error of +/- 1000m, and so the pressure reading is of little practical use
except as a very coarse upper-altitude limit.

If you want to make use of the pressure reading, please refer to the example code provided in _eRIC_CutDown_Tx_Pressure_and_Temperature.zip_ in the
[eRIC folder](https://github.com/PaulZC/Pyrotechnic_Balloon_Cut-Down/tree/master/Archive/V1/eRIC). Programming instructions can be found in
[Making changes to the eRIC code](https://github.com/PaulZC/Pyrotechnic_Balloon_Cut-Down/blob/master/Archive/V1/ASSEMBLY.md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).

### Pyrotechnic output



Q1 is a DMG3415U-7 P-Channel MOSFET which can switch currents of: 4 Amps continuous; 30 Amps pulsed. By default, the Gate of Q1 is held high by R9, which disables
the MOSFET. When the Gate of Q1 is pulled low by Q2, the full battery voltage is connected to the _PYRO+_ terminal, which triggers the electric
match within the pyrotechnic cutter.

Q2 is an NPN transistor. By default, the Base of Q2 is pulled low by R12, which disables the transistor and prevents it from pulling the Gate of Q1 low.
Q2 is enabled when the _FIRE_ signal connected to its Base goes high.

### Dual NOR gate



IC3 is a 7402 dual NOR logic gate. It prevents the _FIRE_ signal from accidentally going high, e.g. when the eRIC goes through a power-up reset. _FIRE_ can only
go high if:
- eRIC Pin17 is high (which provides power to the NOR gates)
- eRIC Pin18 is high
- eRIC Pin19 is low

The Input/Output pins on most microcontrollers go into a floating (high impedance) state during reset and can only be configured as outputs once the
embedded code starts to execute. The 7402 NOR gate ensures that _FIRE_ does not accidentally go high during that period.

### Reset supervisor



IC2 is an MCP111T-240 reset supervisor. It ensures that the eRIC is reset whenever the battery voltage falls below 2.4V.

Normally, the nichrome heating wire inside the electric match will go open-circuit as soon as the match is activated. If this fails to happen, Q1 will continue to
deliver current to the electric match until the batteries are exhausted. IC2 ensures that the eRIC is reset when the battery voltage starts to fall, which in turn
will disable Q1 via IC3 and Q2.

### LEDs

LED1 will illuminate when the PYRO output is active.

LED2 will flash once per second to show that the cut-down is operational. LED2 will be lit continuously when the eRIC is in bootloader mode.

### Diodes

D1 and D2 provide protection for the batteries and USB power pin from each other.

### I/O pins



The eRIC TxD, RxD, CTS and RTS pins are connected to 0.1" pads on the edge of the circuit board. The order of these pads matches the order of the pins of an FTDI
TTL-232R-3V3 USB to TTL serial cable. The eRIC can be reprogrammed via the FTDI cable.

Two extra pads are connected to the eRIC bootloader pins (Pin11 and Pin12). The eRIC will enter bootloader mode if these pads are shorted together on reset
or power-up. LED2 will be lit continuously when the eRIC is in bootloader mode.

### Antennas

Recommended antenna for the eRIC4 is:
- LPRS ANT-SR433 (Farnell part 2096221)

Recommended antenna for the eRIC9 is:
- LPRS ANT-SR900 (Farnell part 2096219)

http://www.lprs.co.uk/products/antennas-cables-connectors/stubby-antennas.html

The horizontal antenna orientation is important if the cut-down is positioned directly above the Iridium Beacon Radio Board on the balloon cord.

### How much does it weigh?



The total weight of the assembled cut-down is 75.4 grams. This comprises:
- Assembled cutter: 27.2g
- Energiser® Ultimate Lithium AAA batteries: 22.7g
- Assembled circuit board: 19.1g
- Antenna: 6.4g

### Which AAA batteries should I use?
Energiser® Ultimate Lithium batteries. These are rated down to -40°C but tests I've done (using dry ice) show that they continue to work much colder than that.

### How long will the batteries last?

With the eRIC power saving set to 2, the average current draw is 4.6mA at 4.5V. When powered by three Energiser® Ultimate Lithium AAA batteries, the batteries
should last approximately 10 days. This ignores the current drawn by the electric match when the cut-down is activated.



### Do I need to be careful around the battery clips?

Yes! The clips are of course conductive. If you place the circuit board battery-side down on a conductive surface **BAD THINGS WILL HAPPEN!**

### Have you tested it?

Yes. The cutter has been used successfully to sever size 4N (2.4mm) braided nylon cord with test loads of 2kg and 100g.





### License

This project is distributed under a Creative Commons Attribution + Share-alike (BY-SA) licence.
Please refer to section 5 of the licence for the "Disclaimer of Warranties and Limitation of Liability".

Enjoy!

**_Paul_**

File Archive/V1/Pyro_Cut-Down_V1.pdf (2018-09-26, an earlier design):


thunderbird\hom e\pclark\D ocum ents\eagle\Pyro_C ut-D ow n\Pyro_C ut-D ow n_V1\Pyro_C ut-D ow n.sch (Sheet: 1/1)


26/09/2018 11:54 \\thunderbird\hom e\pclark\D ocum ents\eagle\Pyro_C ut-D ow n\Pyro_C ut-D ow n_V1\Pyro_C ut-D ow n.brd


26/09/2018 11:55 \\thunderbird\hom e\pclark\D ocum ents\eagle\Pyro_C ut-D ow n\Pyro_C ut-D ow n_V1\Pyro_C ut-D ow n.brd


Part | X | Y | Angle | Package | Value | Manufacturer | Manufacturer Part No | Farnell Part No Mouser Part No | Description
Dimensions 51.44 | 63.50

Fiducials - for solder paste mask alignment:

FD1 | 48.26 | 48.26 | 0 | | | | | | Fiducial 1mm
FD2 | 2.54 | 6.35 | 0 | | | | | | Fiducial 1mm

Surface Mount Components:

C1 | 3.18 | 21.53 | 180 0603 | 1uF | Murata | GRM188R61A105KA61D 1828798 | MultiLayer Ceramic Capacitor; 1uF; 10V; 0603; X5R
C2 | 3.21 | 19.49 | 180 0603 | 0.1uF | Murata | GRM188R71H104JA93D 2688523 | MultiLayer Ceramic Capacitor; 0.1uF; 50V; 0603; X7R
C3 | 22.76 | 31.21 | 90 0603 | 1uF | Murata | GRM188R61A105KA61D 1828798 | MultiLayer Ceramic Capacitor; 1uF; 10V; 0603; X5R
C4 | 36.83 | 10.16 | 0 0603 | 0.1uF | Murata | GRM188R71H104JA93D 2688523 | MultiLayer Ceramic Capacitor; 0.1uF; 50V; 0603; X7R
C5 | 36.83 | 7.62 | 0 0805 | 10uF | Murata | GCJ21BR71A106KE01L | 2781411 | MultiLayer Ceramic Capacitor; 10uF; 10V; 0805; X7R
D1 | 21.59 | 8.76 | 270 SOD-123 | MBR120 | ON SEMICONDUCTOR MBR120VLSFT1G | 1431044 | Schottky Rectifier; 20V; 1A; SOD-123
D2 | 34.99 | 32.23 | 90 SOD-123 | MBR120 | ON SEMICONDUCTOR MBR120VLSFT1G | 1431044 | Schottky Rectifier; 20V; 1A; SOD-123
IC1 | 25.4 | 20.32 | 0 | ERIC4 | LPRS | ERIC4 | 2362439 | LPRS easy Radio Intelligent Controller 433MHz
| | | | | ERIC9 | LPRS | ERIC9 | 2362440 | LPRS easy Radio Intelligent Controller 868/915MHz
IC2 | 44.74 | 9.18 | 0 SOT23-3 | MCP111T-240E/TT | Microchip | MCP111T-240E/TT | 1627192 | Reset Supervisor; SOT23-3; 2.40V; Open Drain; Active Low
IC3 | 18.64 | 32.23 | 270 SOP65P400X130-8N SN74LVC2G02DCTR Texas Instruments | SN74LVC2G02DCTR | 1236358 | NOR Gate, 2 Input, 32 mA, 1.65 V to 5.5 V, SSOP-8
IC4 | 7.49 | 19.65 | 0 LGA8 | MPL3115A2 | NXP | MPL3115A2 | 2009084 | Pressure Sensor
LED1 | 25.15 | 38.16 | 90 2.0x1.25 | RED | Wurth Electronik | 150080RS75000 | 2322077 | 710-150080RS75000 LED; Red; 20mA; 2V; 2.0x1.25mm
LED2 | 27.24 | 31.34 | 180 2.0x1.25 | RED | Wurth Electronik | 150080RS75000 | 2322077 | 710-150080RS75000 LED; Red; 20mA; 2V; 2.0x1.25mm
Q1 | 43.15 | 42.58 | 270 SOT23 | DMG3415U-7 | Diodes Inc. | DMG3415U-7 | 1843688 | MOSFET; P Channel; SOT23-WIDE
Q2 | 33.75 | 41.24 | 270 SOT23 | 2N2222 | Fairchild | MMBT2222A | 9846700 | Bipolar (BJT) Single Transistor, NPN, 40 V, 350 mW, 1 A
R1 | 29.11 | 38.26 | 180 0603 | 2.2K | Multicomp | MCWR06X2201FTL | 2447320 | Chip Resistor; Thick Film; 2.2k; 50V; 0603; 100mW
R2 | 11.27 | 21.88 | 270 0603 | 1K | Multicomp | MCWR06X1001FTL | 2447272 | Chip Resistor; Thick Film; 1k; 50V; 0603; 100mW
R3 | 29.18 | 36.1 | 180 0603 | 100k | Multicomp | MCWR06X1003FTL | 2447226 | Chip Resistor; Thick Film; 100k; 50V; 0603; 100mW
R4 | 11.27 | 18.48 | 90 0603 | 1K | Multicomp | MCWR06X1001FTL | 2447272 | Chip Resistor; Thick Film; 1k; 50V; 0603; 100mW
R5 | 24.07 | 8.51 | 90 0603 | 1K | Multicomp | MCWR06X1001FTL | 2447272 | Chip Resistor; Thick Film; 1k; 50V; 0603; 100mW
R6 | 25.3 | 36.1 | 180 0603 | 100k | Multicomp | MCWR06X1003FTL | 2447226 | Chip Resistor; Thick Film; 100k; 50V; 0603; 100mW
R7 | 25.37 | 31.15 | 90 0603 | 1K | Multicomp | MCWR06X1001FTL | 2447272 | Chip Resistor; Thick Film; 1k; 50V; 0603; 100mW
R8 | 29.15 | 8.51 | 90 0603 | 1K | Multicomp | MCWR06X1001FTL | 2447272 | Chip Resistor; Thick Film; 1k; 50V; 0603; 100mW
R9 | 38.16 | 42.55 | 180 0603 | 10K | Multicomp | MCWR06X1002FTL | 2447230 | Chip Resistor; Thick Film; 10k; 50V; 0603; 100mW
R11 | 21.15 | 38.86 | 0 0603 | 1K | Multicomp | MCWR06X1001FTL | 2447272 | Chip Resistor; Thick Film; 1k; 50V; 0603; 100mW
R12 | 21.18 | 36.1 | 0 0603 | 10K | Multicomp | MCWR06X1002FTL | 2447230 | Chip Resistor; Thick Film; 10k; 50V; 0603; 100mW

Non-surface mount components:

RF | | | | | SMA Jack | Johnson | 142-0711-821 | 1019328 | SMA End Launch Jack
BAT1 | | | | | AAA-Clip_Pair | Keystone Electronics | 82 | 908721 | Keystone Electronics 82 AAA Battery Clip (Pair)
BAT2 | | | | | AAA-Clip_Pair | Keystone Electronics | 82 | 908721 | Keystone Electronics 82 AAA Battery Clip (Pair)
BAT3 | | | | | AAA-Clip_Pair | Keystone Electronics | 82 | 908721 | Keystone Electronics 82 AAA Battery Clip (Pair)
RESET | | | | | Tactile Switch | Multicomp | MCDTS6-1N | 9471685 | Switch, SPST, 0.05A, 12VDC, 160gf
PYRO | | | | | Terminal Block | Phoenix Contact | SPTA 1/2-3.5 | 1793729 | Terminal Block; 3.5mm; 2 Ways; 24-16 AWG

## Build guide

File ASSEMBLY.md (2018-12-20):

# Pyrotechnic Balloon Cut-Down Device

## Circuit Board Assembly and Configuration

A lightweight wireless cut-down device for use on high altitude balloons.



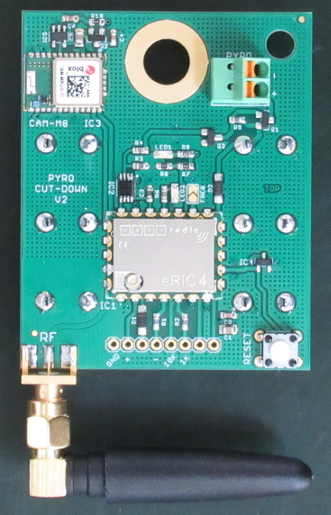
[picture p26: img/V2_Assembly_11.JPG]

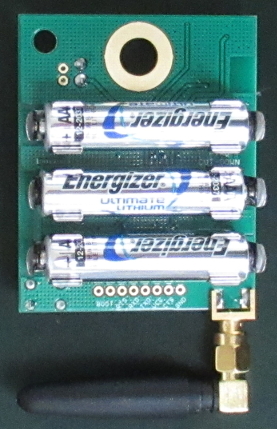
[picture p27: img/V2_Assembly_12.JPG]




Designed to be triggered by the [Iridium Beacon Radio Board](https://github.com/PaulZC/Iridium_Beacon_Radio_Board) and equipped with an
[LPRS eRIC4 or eRIC9 integrated radio module](http://www.lprs.co.uk/products/easyradio-ism-modules/eric-soc-rf-modules.html),
the cut-down will be triggered when the eRIC receives its own (unique) serial number on the chosen channel. The number of cut-downs that could be
triggered by a single Iridium Beacon is essentially unlimited.

**New for V2: the cut-down now includes a u-blox CAM-M8Q GNSS (GPS) receiver and can be configured to trigger at a pre-set altitude.**

The cutter has been designed to sever size 4N (2.4mm) braided nylon cord.

The cut-down device could also be used to control:
- a nichrome hot wire cord cutter
- a strobe or audible alarm
- any other device which can operate from 3.3V to 4.8V (depending on the battery voltage)

See [Pyro_Cut-Down_V2.pdf](https://github.com/PaulZC/Pyrotechnic_Balloon_Cut-Down/blob/master/Pyro_Cut-Down_V2.pdf) for the schematic,
layout and Bill Of Materials.

The [Eagle](https://github.com/PaulZC/Pyrotechnic_Balloon_Cut-Down/tree/master/Eagle) directory contains the schematic and pcb design files.

The [eRIC](https://github.com/PaulZC/Pyrotechnic_Balloon_Cut-Down/tree/master/eRIC) directory contains the code for the eRIC integrated controller.

Here are the assembly and configuration instructions for V2 of the PCB:

### Blank PCB

Start by having the blank PCBs manufactured. If you are based in the UK or Europe, I can recommend
[Multi-CB](https://www.multi-circuit-boards.eu/en/index.html) who can manufacture PCBs in 1-8 working days and
can process the Eagle .brd file direct - there's no need to generate Gerber files.

My recommended options are:
- Layers: 2 layers
- Format: single pieces
- Surface finish: chemical gold (ENIG)
- Material: FR4, 1.55mm
- Cu layers: 35um
- Solder stop: both sides, green
- Marking print: both sides, white

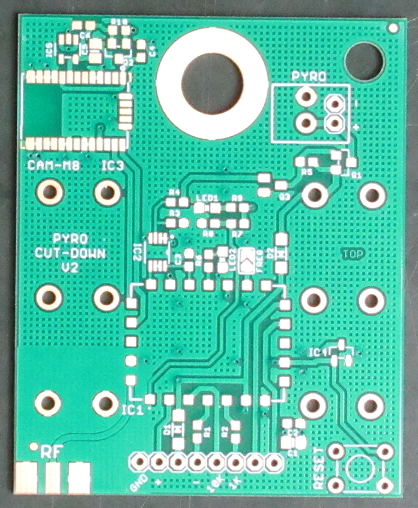
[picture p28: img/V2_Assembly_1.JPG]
V2_Assembly_1


### Add solder paste

Multi-CB can also provide you with a solder paste (SMD) stencil for the PCB. My recommended options are:
- SMD stencil for: top layer
- Type: custom
- Pad reduction: yes, 10%
- Thickness: 100um
- Existing fiducials: lasered through
- Text type: half lasered
- Double-sided brushing: yes

Secure the blank PCB onto a flat work surface by locating it between two engineer's squares. I use a sheet of toughened glass
as the work surface as it is both very flat and easy to clean.

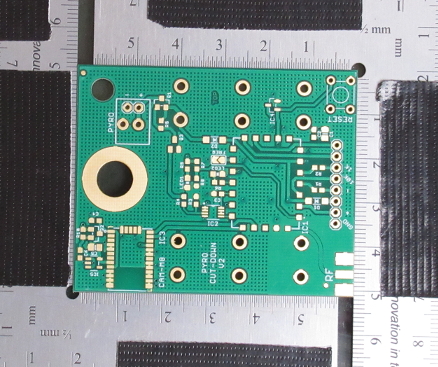
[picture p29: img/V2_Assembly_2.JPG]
V2_Assembly_2


Use the two round fiducials to line up the stencil with the PCB. Secure the stencil with tape.

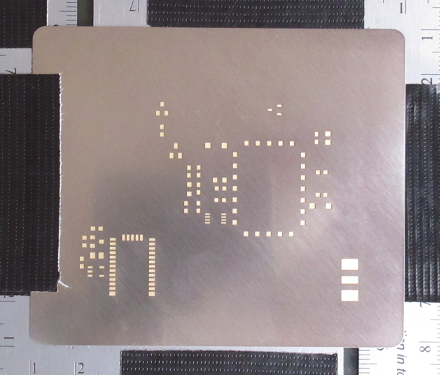
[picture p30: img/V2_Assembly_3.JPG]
V2_Assembly_3


Apply solder paste close to the component cut-outs and then scrape the paste over the stencil using a knife blade
or a similar straight edge. Take appropriate safety precautions when working with solder paste - particularly if you are using
tin-lead solder instead of lead-free.

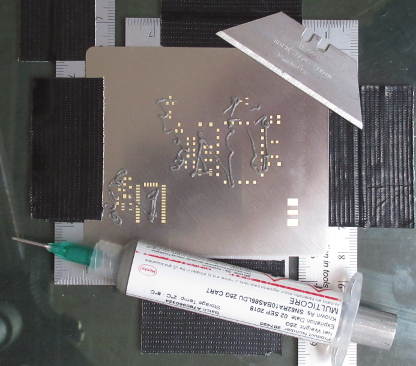
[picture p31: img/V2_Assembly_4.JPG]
V2_Assembly_4


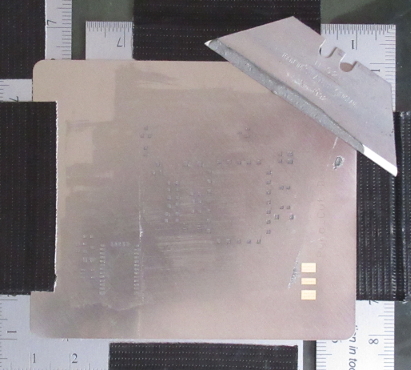
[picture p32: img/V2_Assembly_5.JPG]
V2_Assembly_5


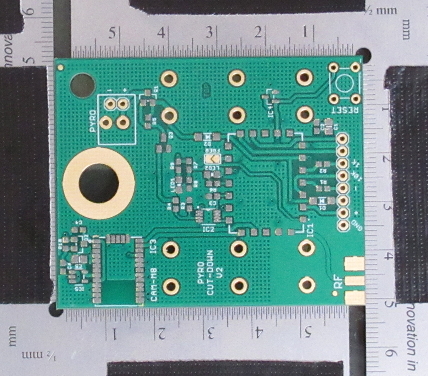
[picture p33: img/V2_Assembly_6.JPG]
V2_Assembly_6


### Position the surface mount components

Position the components onto the blobs of solder paste using tweezers. A magnifier lamp or a USB microscope will
help you place the components in the correct position. IC3 - the u-blox CAM-M8Q - is probably the trickiest
component to position. Take extra time to make sure it is centered accurately on the pads.

### Reflow the surface mount components

Use a reflow oven to heat the circuit board to the correct temperatures to melt the solder. A reflow oven doesn't need to be expensive. The one shown below was assembled from:

- Quest 9L 800W mini-oven
- Inkbird PID temperature controller and 40A solid state relay
- Type K thermocouple

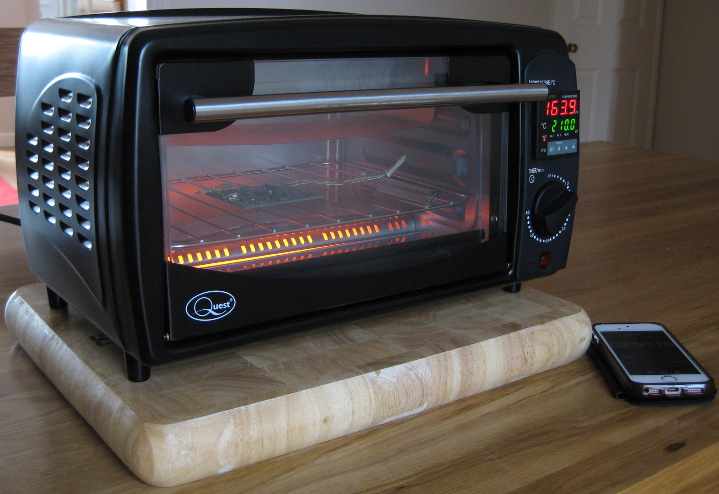
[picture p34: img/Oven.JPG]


Several people have published good reflow oven construction guides, including [this one](http://www.die4laser.com/toaster/index.html).

Use the correct temperature profile for your solder paste, but you won't go far wrong with 160C for four minutes, followed by
210C for one minute, followed by a cool-down with the door open. Use a flashlight to check that the solder has melted across
the whole PCB at 210C. Hold the temperature at 210C a little longer if some of the solder paste still appears 'gray' instead of 'silver'.

All being well, your PCB should look like this:

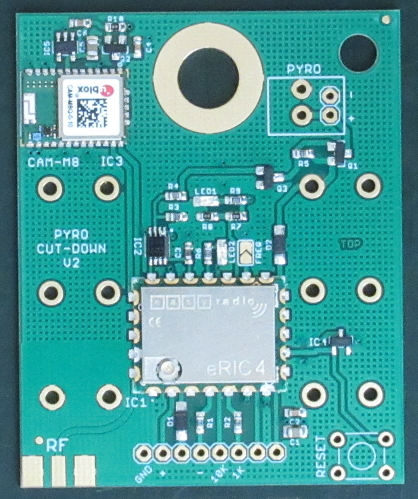
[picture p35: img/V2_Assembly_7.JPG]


### Check for shorts

Carefully examine all the solder joints and correct any shorts you find.

The 'trick' to removing a short is to add more solder or solder paste and then to use
copper solder braid or wick to remove all the solder in one go.

Use a cotton swab dipped in Isopropyl Alcohol (IPA / Propanol / rubbing alcohol) to remove any flux residue.

### Add the non-surface mount components

The non-surface mount components (battery clips, reset switch, pyrotechnic connector, SMA connector) can now be soldered into place.

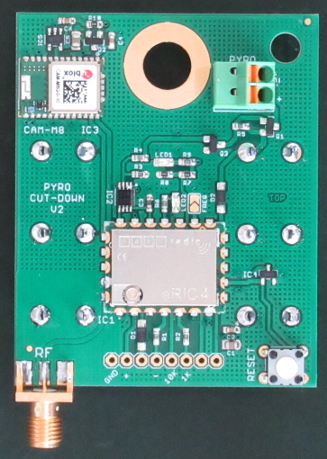
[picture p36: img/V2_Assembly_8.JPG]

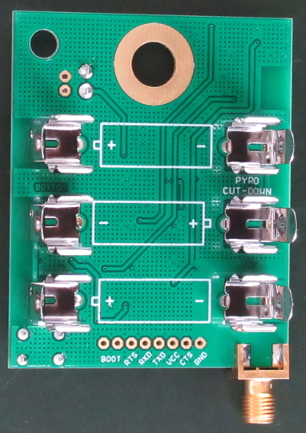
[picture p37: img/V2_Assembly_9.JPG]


### Lacquer the PCB

I do recommend giving the PCB a coat of lacquer, especially if you are intending to use it on a balloon flight.
Cover all of the surface mount components with [Acrylic Protective Lacquer (conformal coating)](https://uk.rs-online.com/web/p/conformal-coatings/3217324/)
taking care to avoid the I/O pins and the reset switch.

### Configure the eRIC

The eRIC will come pre-programmed with easyRadio V1.5.5. This needs to be replaced with the custom code which you will find in the
[eRIC folder](https://github.com/PaulZC/Pyrotechnic_Balloon_Cut-Down/tree/master/eRIC).

You can find the datasheet for the eRIC on the LPRS website:
- http://www.lprs.co.uk/products/easyradio-ism-modules/eric-soc-rf-modules.html
- http://www.lprs.co.uk/assets/files/eRIC4_9_Datasheet_1.34.pdf

Download and install the latest version of the easyRadio Companion:
- http://www.lprs.co.uk/development-tools/easyradio-evaluation-software.html
- http://www.lprs.co.uk/assets/files/easyRadiosetup%204.1.6.exe

If possible, use an FTDI TTL-232R-3V3 cable to reconfigure the board, although a TTL-232R-5V will work too.
- https://www.ftdichip.com/Products/Cables/USBTTLSerial.htm

Plug the 6-Way connector of the FTDI cable onto one end of an 8-way length of double-height 0.1" header strip. Leave the cable USB connector unconnected for now.

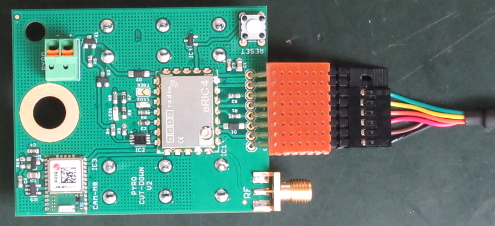
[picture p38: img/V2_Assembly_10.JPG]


Insert the header strip through the holes in the PCB and then lean the header strip against the side of the holes to ensure good electrical contact. Now plug
the FTDI USB connector into your computer. LED2 should be flashing once per second; if it is lit continuously ensure you do not have a jumper link connecting
the two "Boot" pads together. If required, press the Reset button to restart the eRIC.

Start the easyRadio Companion. Registering the software is recommended but is optional. Click on the "eRIC" button. Select the COM port for the FTDI
cable in the UART Settings, then click "Open Port".

Ensure the "Settings" vertical tab is selected.

Click on the "Module Info" horizontal tab. Click on "Discover Module". Wait for all of the module information to be collected. Make a note of the eight digit
eRIC serial number; you will need this to be able to trigger the cut-down. Ideally, print the serial number onto a label and stick it onto the eRIC.

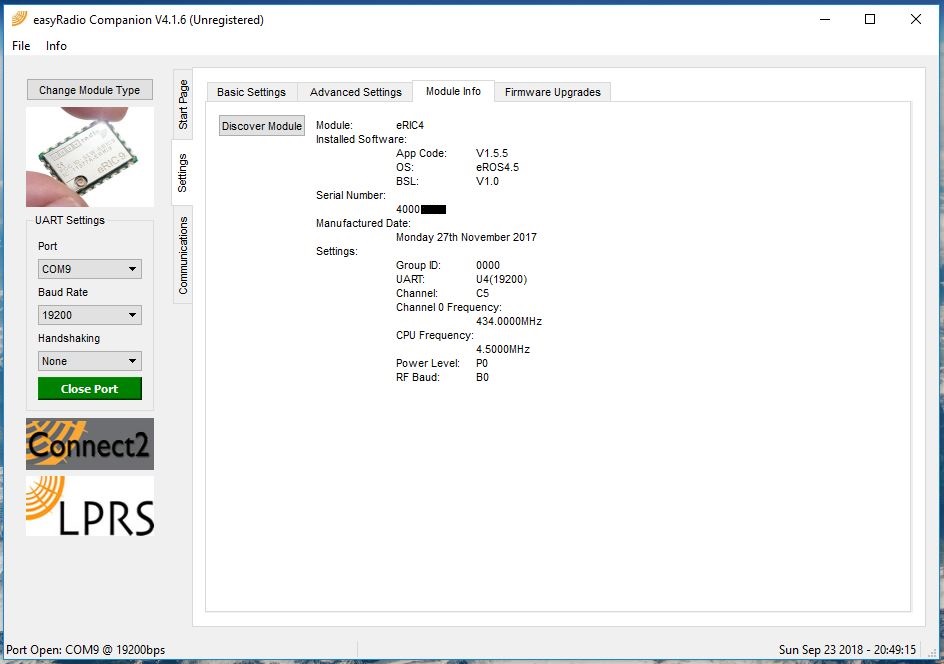
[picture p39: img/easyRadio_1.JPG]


Place a jumper link to link the two "Boot" header pins together; then press the Reset button to place the eRIC into bootloader mode. LED2 should light up
continuously. If LED2 is flashing once per second instead, ensure you have the jumper link installed correctly. If required, press the Reset button to restart
the eRIC.

Click on the "Firmware Upgrades" horizontal tab. Click on "Open Firmware File" and browse to the eRIC4_Pyro_CutDown_V2.hex file which you will find in the
[eRIC folder](https://github.com/PaulZC/Pyrotechnic_Balloon_Cut-Down/tree/master/eRIC). Select eRIC9_Pyro_CutDown_V2.hex instead if you are using the 868 / 915MHz
eRIC9.

Leave "Enable Code Protect" selected and then click "Upgrade".

All being well, you should see a green progress bar followed by the message "Firmware Update Complete!".

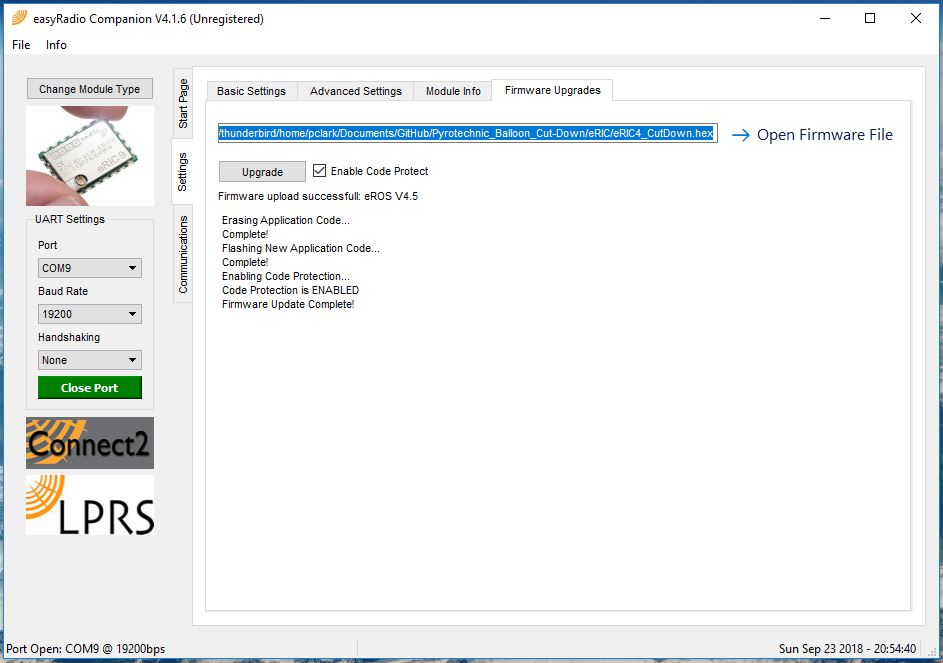
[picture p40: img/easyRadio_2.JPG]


Disconnect the FTDI USB connector from your computer, then remove the header strip.

### Making changes to the eRIC code

If you want to alter the programming of the eRIC, you will need to:
- Follow the instructions in http://www.lprs.co.uk/assets/files/Custom%20programming%20eRIC.zip
- Install the Texas Instruments Code Composer Studio
- Copy and unzip the eRIC_Pyro_CutDown_V2.zip from the [eRIC folder](https://github.com/PaulZC/Pyrotechnic_Balloon_Cut-Down/tree/master/eRIC) into the Code Composer workspace directory
- Right-click in the Project Explorer window, select "Import" then "CCS Projects"
- Select the folder which you unzipped eRIC_CutDown into

You can now make alterations to the code, rebuild the project to produce a new .hex file and then use the easyRadio Companion to programme the eRIC with the new code.

### License

This project is distributed under a Creative Commons Attribution + Share-alike (BY-SA) licence.
Please refer to section 5 of the licence for the "Disclaimer of Warranties and Limitation of Liability".

Enjoy!

**_Paul_**

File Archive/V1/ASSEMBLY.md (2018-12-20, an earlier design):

# Pyrotechnic Balloon Cut-Down Device

## Circuit Board Assembly and Configuration

A lightweight wireless cut-down device for use on high altitude balloons.

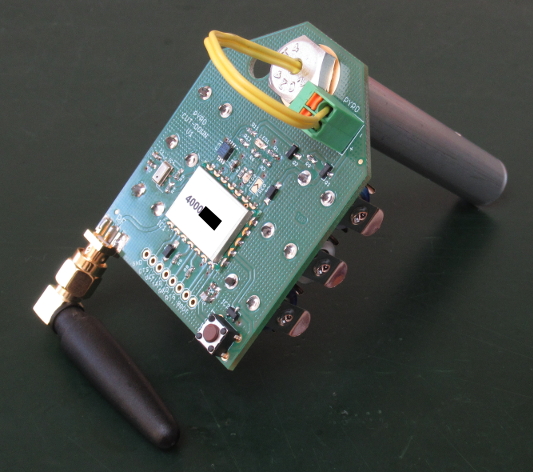
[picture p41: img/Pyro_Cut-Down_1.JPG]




Designed to be triggered by the [Iridium Beacon Radio Board](https://github.com/PaulZC/Iridium_Beacon_Radio_Board) and equipped with an
[LPRS eRIC4 or eRIC9 integrated radio module](http://www.lprs.co.uk/products/easyradio-ism-modules/eric-soc-rf-modules.html),
the cut-down will be triggered when the eRIC receives its own (unique) serial number on the chosen channel. The number of cut-downs that could be
triggered by a single Iridium Beacon is essentially unlimited.

The cutter has been designed to sever size 4N (2.4mm) braided nylon cord.

The cut-down device could also be used to control:
- a nichrome hot wire cord cutter
- a strobe or audible alarm
- any other device which can operate from 3.3V to 4.8V (depending on the battery voltage)

See [Pyro_Cut-Down_V1.pdf](https://github.com/PaulZC/Pyrotechnic_Balloon_Cut-Down/blob/master/Archive/V1/Pyro_Cut-Down_V1.pdf) for the schematic,
layout and Bill Of Materials.

The [Eagle](https://github.com/PaulZC/Pyrotechnic_Balloon_Cut-Down/tree/master/Archive/V1/Eagle) directory contains the schematic and pcb design files.

The [eRIC](https://github.com/PaulZC/Pyrotechnic_Balloon_Cut-Down/tree/master/Archive/V1/eRIC) directory contains the code for the eRIC integrated controller.

Here are the assembly and configuration instructions for V1 of the PCB:

### Blank PCB

Start by having the blank PCBs manufactured. If you are based in the UK or Europe, I can recommend
[Multi-CB](https://www.multi-circuit-boards.eu/en/index.html) who can manufacture PCBs in 1-8 working days and
can process the Eagle .brd file direct - there's no need to generate Gerber files.

My recommended options are:
- Layers: 2 layers
- Format: single pieces
- Surface finish: chemical gold (ENIG)
- Material: FR4, 1.55mm
- Cu layers: 35um
- Solder stop: both sides, green
- Marking print: both sides, white

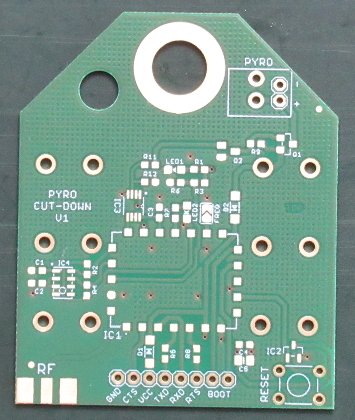
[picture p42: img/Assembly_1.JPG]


### MPL3115A2

IC4 is an MPL3115A2 pressure and temperature sensor. Installing it is optional since:
- Its accuracy degrades above 15km
- The default version of the cut-down code does not use it

The MPL3115A2 is the only component on the PCB that needs to be reflowed: either in a reflow oven; or by hand using a hot air gun. If you do decide to
install it, you can use a toothpick or cocktail stick to apply a small amount of solder paste to each of the eight pads on the PCB. Use an illuminated
magnifier and tweezers to install the package in the correct position before applying heat.

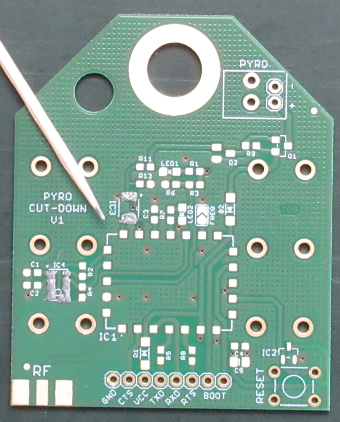
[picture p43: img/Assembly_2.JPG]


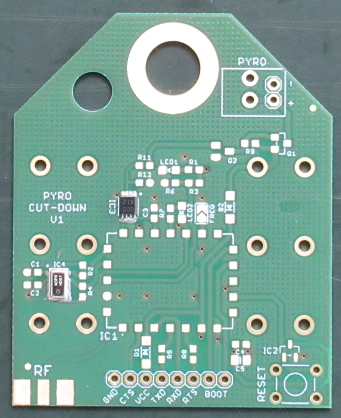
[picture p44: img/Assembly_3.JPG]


A reflow oven doesn't need to be expensive. The one shown below was assembled from:

- Quest 9L 800W mini-oven
- Inkbird PID temperature controller and 40A solid state relay
- Type K thermocouple



Several people have published good reflow oven construction guides, including [this one](http://www.die4laser.com/toaster/index.html).

Use the correct temperature profile for your solder paste, but you won't go far wrong with 160C for four minutes, followed by
210C for one minute, followed by a cool-down with the door open. Use a flashlight to check that the solder has melted across
the whole PCB at 210C. Hold the temperature at 210C a little longer if some of the solder paste still appears 'gray' instead of 'silver'.

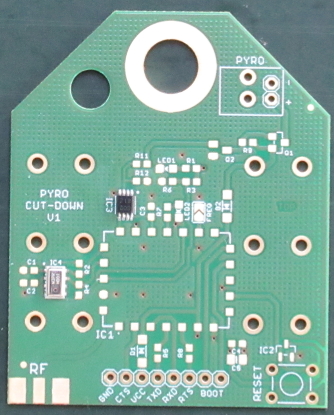
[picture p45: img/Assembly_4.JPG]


Carefully examine the solder paste joints and correct any shorts you find. The 'trick' to removing a short is to add more solder or solder
paste and then to use copper solder braid or wick to remove all the solder in one go.

If you decide to omit the MPL3115A2, you can omit C1, C2, R2 and R4 too.

### Add the rest of the surface mount components

Solder the remaining surface mount components by hand. There are many good surface mount soldering guides available on the web, including
[this one](https://www.youtube.com/watch?v=QzoPxvIM2qE).

Use a cotton swab dipped in Isopropyl Alcohol (IPA / Propanol / rubbing alcohol) to remove any flux residue.

All being well, your PCB should look like this:

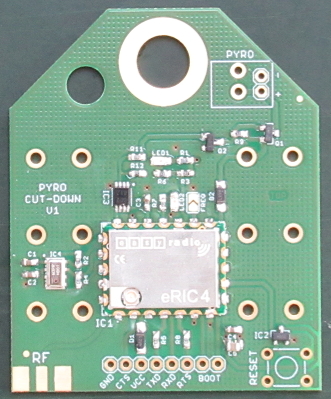
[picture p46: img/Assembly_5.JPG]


### Add the non-surface mount components

The non-surface mount components (battery clips, reset switch, pyrotechnic connector, SMA connector) can now be soldered into place.

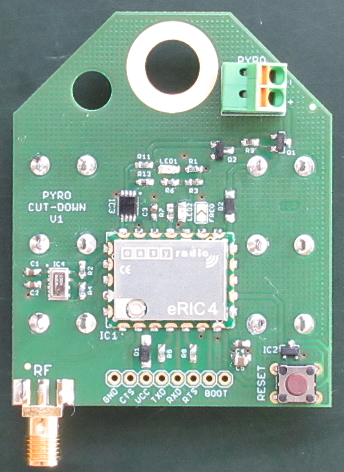
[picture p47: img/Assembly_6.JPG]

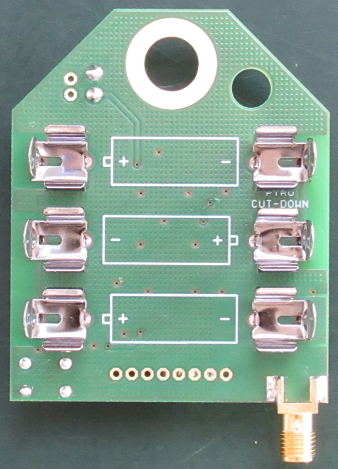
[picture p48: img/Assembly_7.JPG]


### Lacquer the PCB

I do recommend giving the PCB a coat of lacquer, especially if you are intending to use it on a balloon flight.
Cover all of the surface mount components with [Acrylic Protective Lacquer (conformal coating)](https://uk.rs-online.com/web/p/conformal-coatings/3217324/)
except IC4 (pressure sensor).

### Configure the eRIC

The eRIC will come pre-programmed with easyRadio V1.5.5. This needs to be replaced with the custom code which you will find in the
[eRIC folder](https://github.com/PaulZC/Pyrotechnic_Balloon_Cut-Down/tree/master/Archive/V1/eRIC).

You can find the datasheet for the eRIC on the LPRS website:
- http://www.lprs.co.uk/products/easyradio-ism-modules/eric-soc-rf-modules.html
- http://www.lprs.co.uk/assets/files/eRIC4_9_Datasheet_1.34.pdf

Download and install the latest version of the easyRadio Companion:
- http://www.lprs.co.uk/development-tools/easyradio-evaluation-software.html
- http://www.lprs.co.uk/assets/files/easyRadiosetup%204.1.6.exe

If possible, use an FTDI TTL-232R-3V3 cable to reconfigure the board, although a TTL-232R-5V will work too.
- https://www.ftdichip.com/Products/Cables/USBTTLSerial.htm

Plug the 6-Way connector of the FTDI cable onto one end of an 8-way length of double-height 0.1" header strip. Leave the cable USB connector unconnected for now.

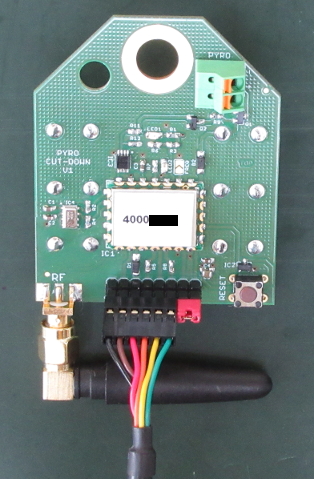
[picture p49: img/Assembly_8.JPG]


Insert the header strip through the holes in the PCB and then lean the header strip against the side of the holes to ensure good electrical contact. Now plug
the FTDI USB connector into your computer. LED2 should be flashing once per second; if it is lit continuously ensure you do not have a jumper link connecting
the two "Boot" pads together. If required, press the Reset button to restart the eRIC.

Start the easyRadio Companion. Registering the software is recommended but is optional. Click on the "eRIC" button. Select the COM port for the FTDI
cable in the UART Settings, then click "Open Port".

Ensure the "Settings" vertical tab is selected.

Click on the "Module Info" horizontal tab. Click on "Discover Module". Wait for all of the module information to be collected. Make a note of the eight digit
eRIC serial number; you will need this to be able to trigger the cut-down. Ideally, print the serial number onto a label and stick it onto the eRIC.



Place a jumper link to link the two "Boot" header pins together; then press the Reset button to place the eRIC into bootloader mode. LED2 should light up
continuously. If LED2 is flashing once per second instead, ensure you have the jumper link installed correctly. If required, press the Reset button to restart
the eRIC.

Click on the "Firmware Upgrades" horizontal tab. Click on "Open Firmware File" and browse to the eRIC4_Pyro_Cut-Down.hex file which you will find in the
[eRIC folder](https://github.com/PaulZC/Pyrotechnic_Balloon_Cut-Down/tree/master/Archive/V1/eRIC). Select eRIC9_Pyro_Cut-Down.hex instead if you are using the 868 / 915MHz
eRIC9.

Leave "Enable Code Protect" selected and then click "Upgrade".

All being well, you should see a green progress bar followed by the message "Firmware Update Complete!".



Disconnect the FTDI USB connector from your computer, then remove the header strip.

### Making changes to the eRIC code

If you want to alter the programming of the eRIC, you will need to:
- Follow the instructions in http://www.lprs.co.uk/assets/files/Custom%20programming%20eRIC.zip
- Install the Texas Instruments Code Composer Studio
- Copy and unzip the eRIC_Pyro_CutDown.zip from the [eRIC folder](https://github.com/PaulZC/Pyrotechnic_Balloon_Cut-Down/tree/master/Archive/V1/eRIC) into the Code Composer workspace directory
- Right-click in the Project Explorer window, select "Import" then "CCS Projects"
- Select the folder which you unzipped eRIC_CutDown into

You can now make alterations to the code, rebuild the project to produce a new .hex file and then use the easyRadio Companion to programme the eRIC with the new code.

If you want to make use of the MPL3115A2 pressure sensor, eRIC_Pyro_CutDown_Tx_Pressure_and_Temperature.zip in the [eRIC folder](https://github.com/PaulZC/Pyrotechnic_Balloon_Cut-Down/tree/master/Archive/V1/eRIC)
contains example code which will read and transmit the pressure and temperature.

### License

This project is distributed under a Creative Commons Attribution + Share-alike (BY-SA) licence.
Please refer to section 5 of the licence for the "Disclaimer of Warranties and Limitation of Liability".

Enjoy!

**_Paul_**

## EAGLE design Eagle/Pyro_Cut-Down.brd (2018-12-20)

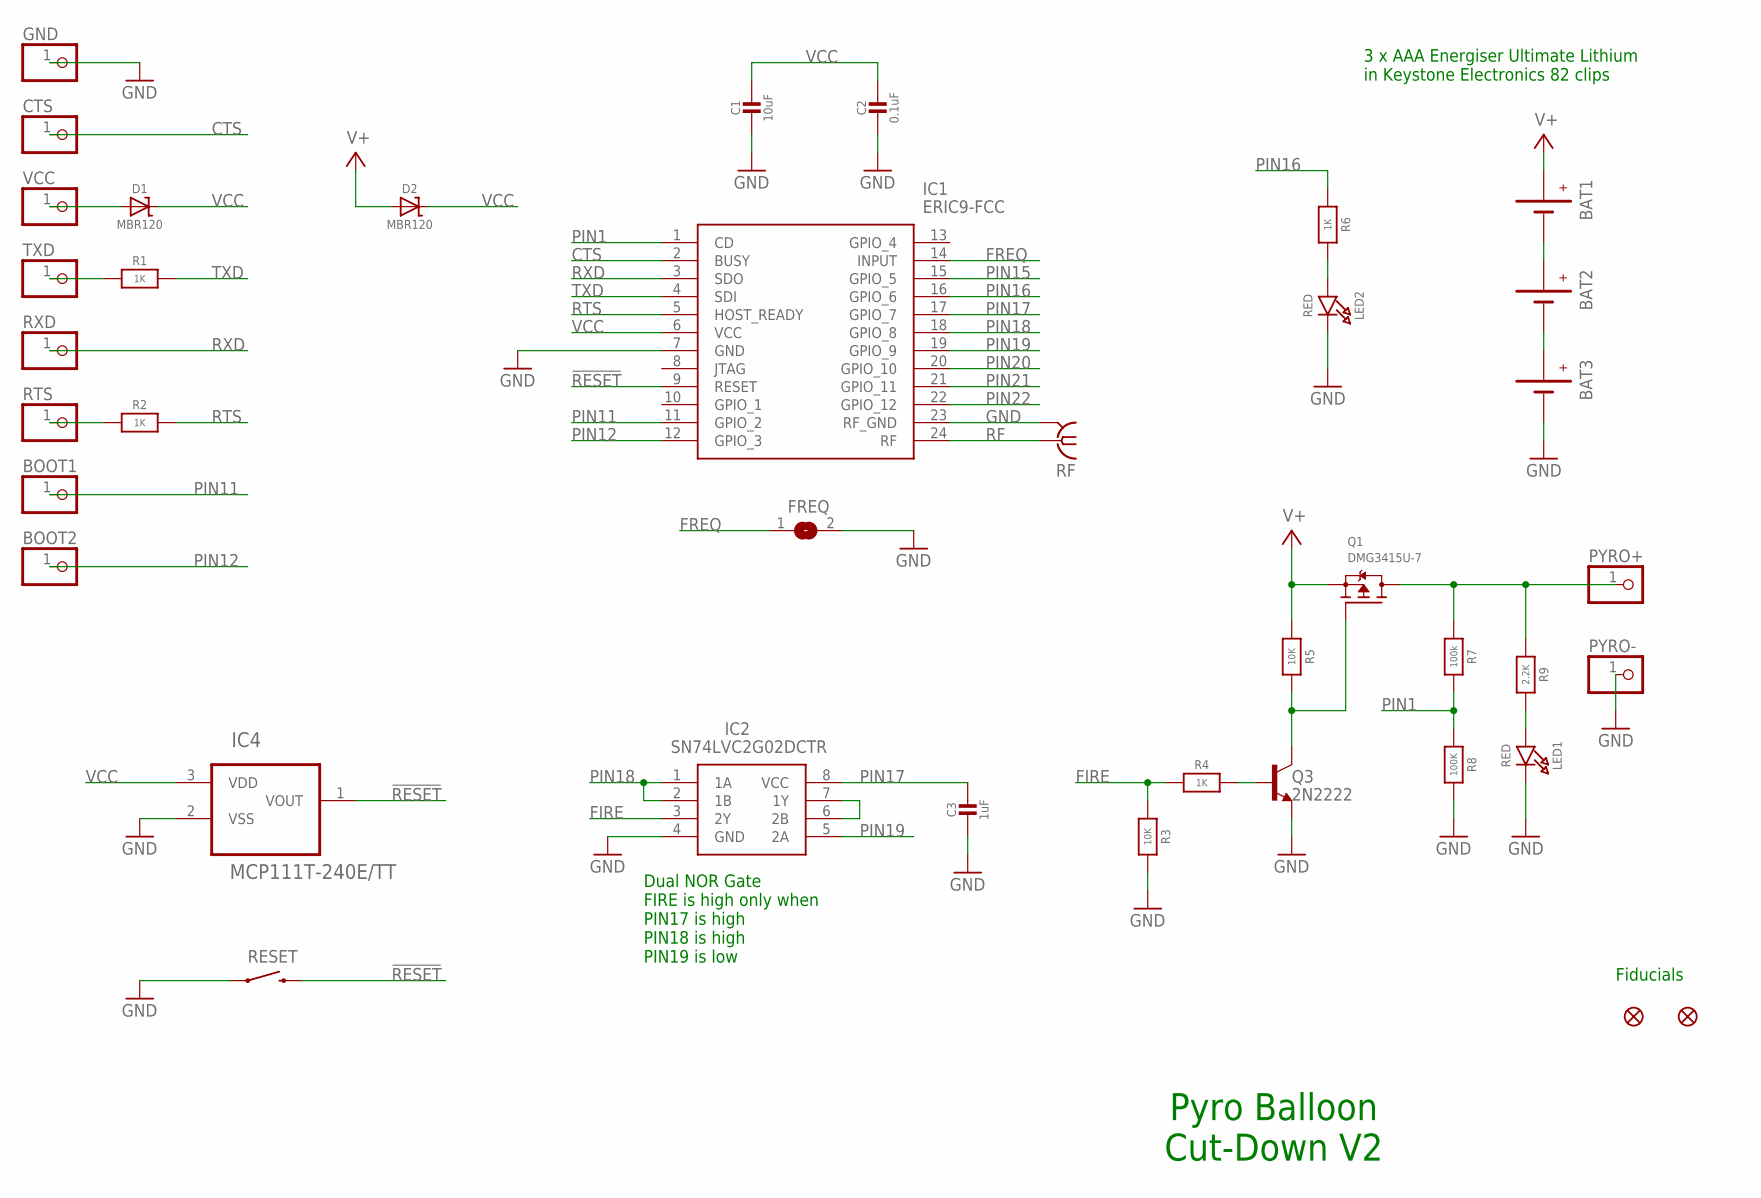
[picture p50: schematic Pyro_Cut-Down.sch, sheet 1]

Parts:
BAT1, BAT2, BAT3: BATTERYKEYSTONE82; BATTERY-AAA-KEYSTONE82
BOOT1, BOOT2: PINHD-1X1; 1X01
C1: 10uF; 0805-NO
C2: 0.1uF; 0603-NO
C3: 1uF; 0603-NO
CTS: PINHD-1X1; 1X01
D1, D2: MBR120; SOD-123
FD1, FD2: FIDUCIAL1X2; FIDUCIAL-1X2
FREQ: SOLDERJUMPER; SOLDERJUMPER_ARROW_NOPASTE
GND: PINHD-1X1; 1X01
IC1: ERIC9-FCC; ERIC4
IC2: SN74LVC2G02DCTR; SOP65P400X130-8N
IC4: MCP111T-240E/TT; SOT95P237X112-3N; MPN MCP111T-240E/TT
LED1, LED2: RED; CHIPLED_0805_NOOUTLINE
PYRO+: PINHD-1X1; 1X01
PYRO-: PINHD-1X1; 1X01
Q1: DMG3415U-7; SOT23-WIDE
Q3: 2N2222; SOT23-BEC
R1, R2, R4, R6: 1K; 0603-NO
R3, R5: 10K; 0603-NO
R7: 100k; 0603-NO
R8: 100K; 0603-NO
R9: 2.2K; 0603-NO
RESET: SWITCH-MOMENTARY-2PTH; TACTILE-PTH
RF: SMA-142-0711-821/826; J502-ND-142-0711-821/826
RTS: PINHD-1X1; 1X01
RXD: PINHD-1X1; 1X01
TXD: PINHD-1X1; 1X01
VCC: PINHD-1X1; 1X01

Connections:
!RESET: IC1.9 (RESET), IC4.1 (VOUT), RESET.3 (2); also elsewhere on the board
CTS: CTS.1, IC1.2 (BUSY)
FIRE: IC2.3 (2Y), R3.1, R4.1
FREQ: FREQ.1, IC1.14 (INPUT)
GND: BAT3.GND@1 (-), BAT3.GND@2 (-), C1.2, C2.2, C3.2, FREQ.2, GND.1, IC1.7 (GND), IC1.23 (RF_GND), IC2.4 (GND), IC4.2 (VSS), LED1.C, LED2.C, PYRO-.1, Q3.E, R3.2, R8.2, RESET.1, RF.G@1 (2), RF.G@2 (2), RF.G@3 (2), RF.G@4 (2); also elsewhere on the board
unnamed: BAT2.GND@1 (-), BAT2.GND@2 (-), BAT3.PWR@1 (+), BAT3.PWR@2 (+)
unnamed: LED2.A, R6.2
unnamed: BAT1.GND@1 (-), BAT1.GND@2 (-), BAT2.PWR@1 (+), BAT2.PWR@2 (+)
unnamed: LED1.A, R9.2
unnamed: R1.1, TXD.1
unnamed: IC2.6 (2B), IC2.7 (1Y)
unnamed: R2.1, RTS.1
unnamed: D1.A, VCC.1
unnamed: Q1.1 (G), Q3.C, R5.2
unnamed: Q3.B, R4.2
PIN1: IC1.1 (CD), R7.2, R8.1
PIN11: BOOT1.1, IC1.11 (GPIO_2)
PIN12: BOOT2.1, IC1.12 (GPIO_3)
PIN15: IC1.15 (GPIO_5); also elsewhere on the board
PIN16: IC1.16 (GPIO_6), R6.1
PIN17: C3.1, IC1.17 (GPIO_7), IC2.8 (VCC)
PIN18: IC1.18 (GPIO_8), IC2.1 (1A), IC2.2 (1B)
PIN19: IC1.19 (GPIO_9), IC2.5 (2A)
PIN20: IC1.20 (GPIO_10); also elsewhere on the board
PIN21: IC1.21 (GPIO_11); also elsewhere on the board
PIN22: IC1.22 (GPIO_12)
PYRO: PYRO+.1, Q1.3 (D), R7.1, R9.1
RF: IC1.24 (RF), RF.1
RTS: IC1.5 (HOST_READY), R2.2
RXD: IC1.3 (SDO), RXD.1
TXD: IC1.4 (SDI), R1.2
V+: BAT1.PWR@1 (+), BAT1.PWR@2 (+), D2.A, Q1.2 (S), R5.1
VCC: C1.1, C2.1, D1.C, D2.C, IC1.6 (VCC), IC4.3 (VDD); also elsewhere on the board

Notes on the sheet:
3 x AAA Energiser Ultimate Lithium in Keystone Electronics 82 clips
Pyro Balloon Cut-Down V2
Fiducials
Dual NOR Gate FIRE is high only when PIN17 is high PIN18 is high PIN19 is low

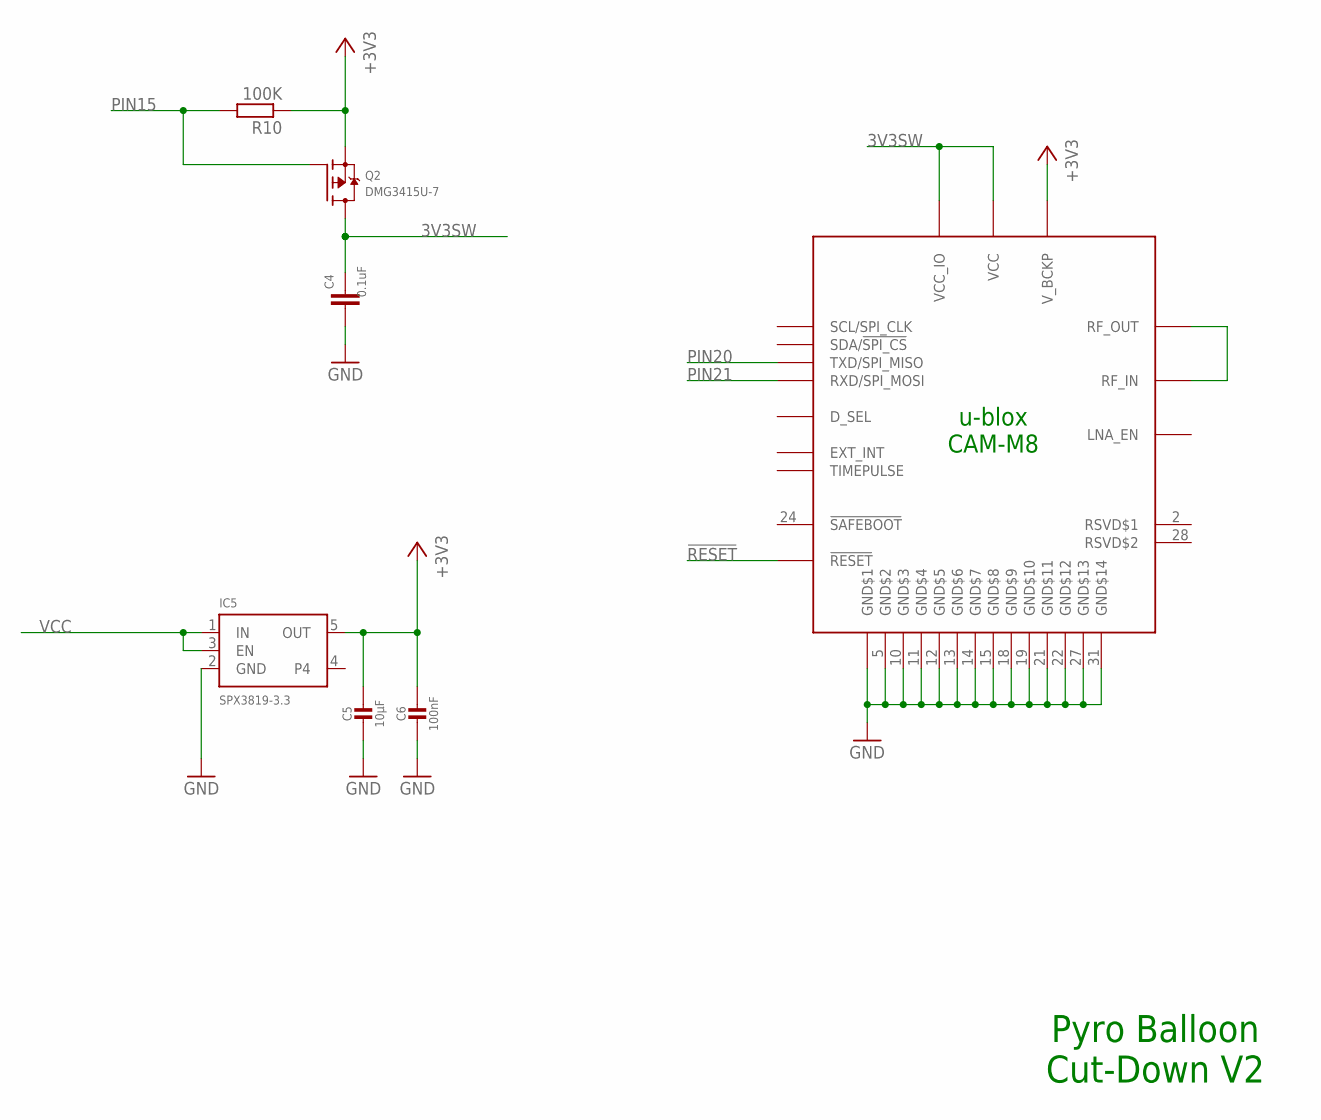
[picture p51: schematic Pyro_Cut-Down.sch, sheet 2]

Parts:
C4: 0.1uF; C0603
C5: 10µF; 0805-NO
C6: 100nF; 0603-NO
IC3: CAM-M8
IC5: SPX3819-3.3; SOT23-5
Q2: DMG3415U-7; SOT23-WIDE
R10: 100K; R0603

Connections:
3V3SW: C4.1, IC3.1 (VCC_IO), IC3.9 (VCC), Q2.3 (D)
!RESET: IC3.23 (!RESET); also elsewhere on the board
+3V3: C5.1, C6.1, IC3.8 (V_BCKP), IC5.5 (OUT), Q2.2 (S), R10.1
GND: C4.2, C5.2, C6.2, IC3.4 (GND$1), IC3.5 (GND$2), IC3.10 (GND$3), IC3.11 (GND$4), IC3.12 (GND$5), IC3.13 (GND$6), IC3.14 (GND$7), IC3.15 (GND$8), IC3.18 (GND$9), IC3.19 (GND$10), IC3.21 (GND$11), IC3.22 (GND$12), IC3.27 (GND$13), IC3.31 (GND$14), IC5.2 (GND); also elsewhere on the board
unnamed: IC3.16 (RF_OUT), IC3.17 (RF_IN)
PIN15: Q2.1 (G), R10.2; also elsewhere on the board
PIN20: IC3.25 (TXD/SPI_MISO); also elsewhere on the board
PIN21: IC3.26 (RXD/SPI_MOSI); also elsewhere on the board
VCC: IC5.1 (IN), IC5.3 (EN); also elsewhere on the board

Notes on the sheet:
u-blox CAM-M8
Pyro Balloon Cut-Down V2

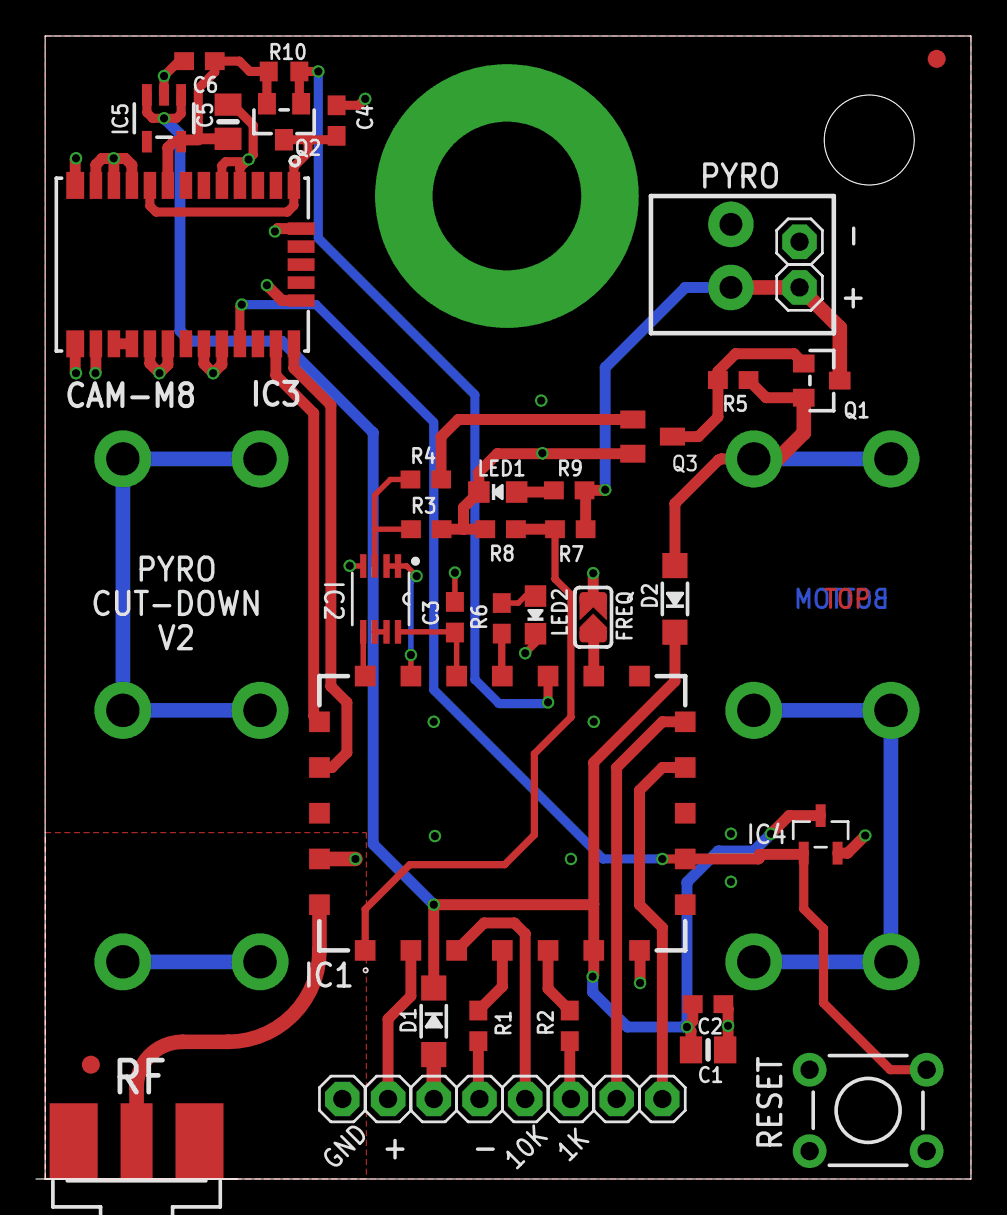
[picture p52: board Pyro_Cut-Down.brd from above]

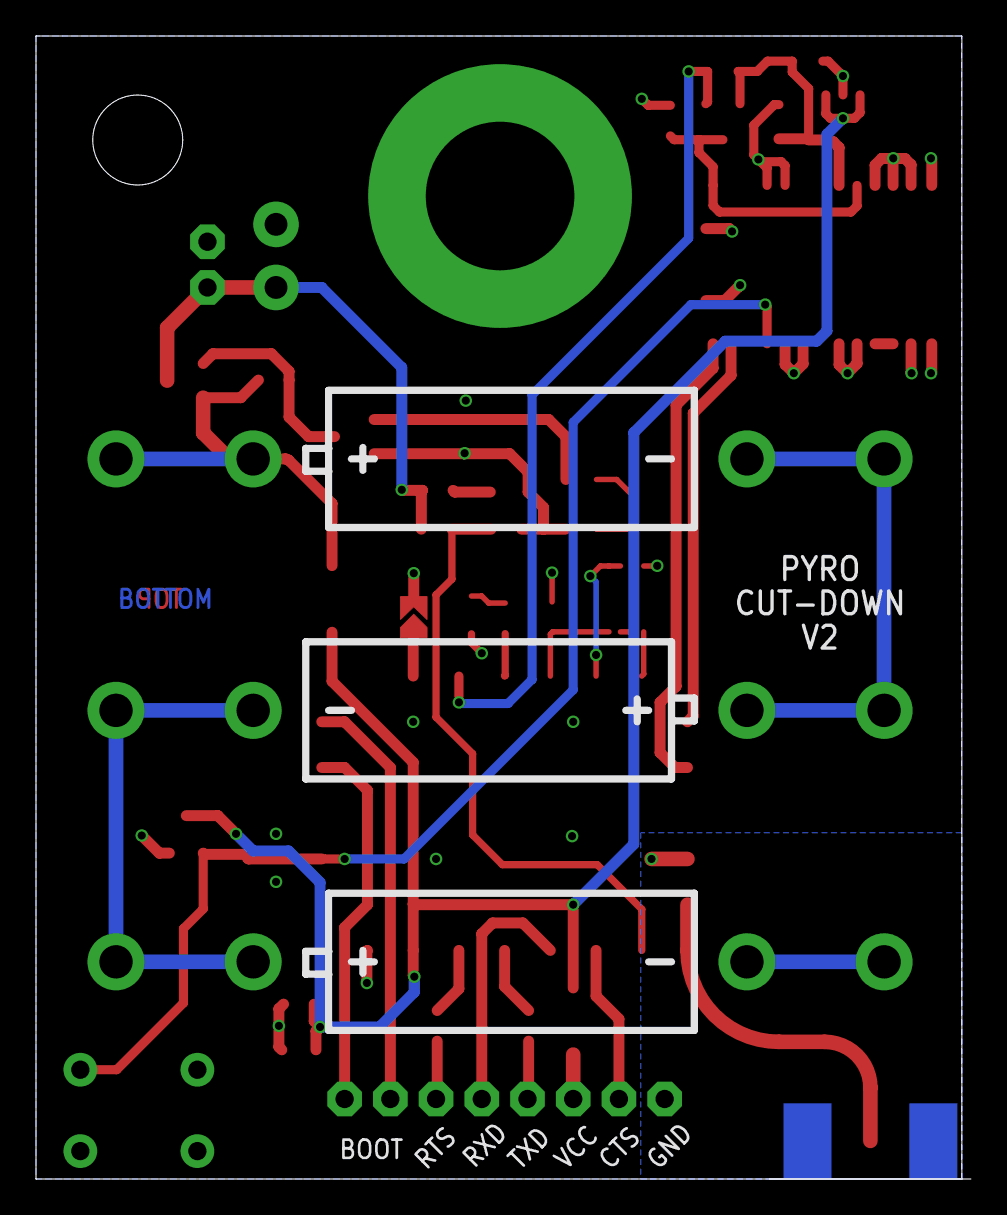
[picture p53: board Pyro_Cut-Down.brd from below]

Board: 2 copper layers, 51.9 x 63.5 mm, 46 parts (3 on the bottom side), 35 nets.

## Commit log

2018-09-24 First release
    [Pyro_Cut-Down.brd, Pyro_Cut-Down.sch]
2018-12-20 Major update for V2
    Major update for V2 of the PCB. Now includes a u-blox CAM-M8Q to provide accurate altitude data. Trigger-at-altitude is now possible.
    [Pyro_Cut-Down.brd, Pyro_Cut-Down.sch]

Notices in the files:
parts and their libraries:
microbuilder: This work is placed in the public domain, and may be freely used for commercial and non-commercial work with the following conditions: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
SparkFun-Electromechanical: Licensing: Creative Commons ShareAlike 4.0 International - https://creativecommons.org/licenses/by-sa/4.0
